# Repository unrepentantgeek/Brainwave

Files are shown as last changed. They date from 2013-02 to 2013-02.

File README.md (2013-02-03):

Description
===========
Brainwave is a low cost controller for Reprap 3D printers derived from the well known Sanguinololu. The primary design goal was lower cost, achieved by providing only the minimum required components for a single extruder printer.  It can be used to drive a cartesian or delta style printer.

Features:
- Small footprint: only 60mm x 79mm!
- 12V power input
- Micro USB connector
- All connectors at edge of board, vertical or right-angle connectors will fit..
- Atmel AT90USB646 microcontroller w/ USB bootloader
- 1, 2, 16 or 32x microstepping @ up to 800mA
- Dual Z-axis connectors
- Optional per channel current attenuation
- Heated bed support with separate power input (up to 24V @ 15A)
- Integrated heater/thermistor/stepper connector for E channel
- Fan control

Instructions
============
1. Build, buy or borrow a Brainwave
2. Install Arduino 1.0.2
3. install the brainwave arduino hardware bundle from
   [github.com/unrepentantgeek/brainwave-arduino](http://github.com/unrepentantgeek/brainwave-arduino)
   into the Arduino hardware directory.
4. Get Marlin. I am maintaining a branch of Marlin that will compile for
   brainwave at [github.com/unrepentantgeek/Marlin](http://github.com/unrepentantgeek/Marlin/tree/brainwave)
   Marlin HEAD has support, but it doesn't always compile cleanly for this
   board.

Hardware configuration
----------------------
1. Set micro-stepping selector jumpers (D1, D2) per channel.  Short both for 32x
   microstepping.  See table on back of board for other configurations.
   <b>Default: single-step.</b>
2. Set stepper current reference voltages.  I = V / 2.55
   <b>Default: 1V == 400mA.</b>

Software configuration
----------------------

Open Arduino, find the Marlin directory and open Marlin.ino. Select 'Brainwave'
from the Board menu. Find the Configuration.h file and change
DEFAULT_AXIS_STEPS_PER_UNIT to suit your printer (remember, 32x microsteps!)
Power on the Brainwave and connect the USB cable (note: the brainwave will not
power up off USB, you need the 12V supply.) Hold down the PROGRAM button and
press RESET, the STATUS led should pulse. Press the Upload button in Arduino.
After a reset the brainwave will show up as a CDC ACM serial device
(/dev/ttyACM[0..9] on Linux) and be ready to accept commands.

Brandon Bowman wrote up an excellent guide for getting the board working under
Windows and MacOS:
[fabbersuw.blogspot.com/2012/12/if-your-brainwaves-got-no-brains-or.html](http://fabbersuw.blogspot.com/2012/12/if-your-brainwaves-got-no-brains-or.html)

Known issues
------------
- It may take a couple of presses of the RESET button to get the firmware to
  come up after flashing.
- You may need a thermistor or similar 100k resistance present across the bed
  and extruder thermistor inputs. Otherwise Marlin may go into a deathloop and
  you'll never even see a serial device. Even if it doesn't fall on it's face it
  will only sit and complain about too high temp.
- Marlin may lose/gain steps on the X axis.  If so swap X and E to limit the
  impact.  This has not been observed with Sprinter.  The issue is being
  investigated.

Special thanks
--------------
Julie Atwood
Matt Westervelt
Frederik Hubinette
Silas Snider
Johann Rocholl
JP Sugarbroad
Austin Appleby
Richard DeLeon
Plamena Milusheva
Mark Ganter
Brandon Bowman

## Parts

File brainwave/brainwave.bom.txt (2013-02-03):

Part     Value             Device             Package         Description                                                            
BED_TEMP                   JP1E               JP1             JUMPER                                                                 
C1       220pF             C-EUC0603          C0603           CAPACITOR, European symbol                                             
C2       10pF              C-EUC0603          C0603           CAPACITOR, European symbol                                             
C3       10pF              C-EUC0603          C0603           CAPACITOR, European symbol                                             
C4       1uF               C-USC0603          C0603           CAPACITOR, American symbol                                             
C5       0.1uF             C-EUC0603          C0603           CAPACITOR, European symbol                                             
C6       0.1uF             C-EUC0603          C0603           CAPACITOR, European symbol                                             
C7       220pF             C-EUC0603          C0603           CAPACITOR, European symbol                                             
C8       10uF              CPOL-US153CLV-0505 153CLV-0505     POLARIZED CAPACITOR, American symbol                                   
C9       0.1uF             C-EUC0603          C0603           CAPACITOR, European symbol                                             
C10      0.1uF             C-EUC0603          C0603           CAPACITOR, European symbol                                             
C11      10uF              CPOL-US153CLV-0505 153CLV-0505     POLARIZED CAPACITOR, American symbol                                   
C12      220pF             C-EUC0603          C0603           CAPACITOR, European symbol                                             
C13      0.1uF             C-EUC0603          C0603           CAPACITOR, European symbol                                             
C14      0.1uF             C-EUC0603          C0603           CAPACITOR, European symbol                                             
C15      10uF              CPOL-US153CLV-0505 153CLV-0505     POLARIZED CAPACITOR, American symbol                                   
C16      220pF             C-EUC0603          C0603           CAPACITOR, European symbol                                             
C17      0.1uF             C-EUC0603          C0603           CAPACITOR, European symbol                                             
C18      0.1uF             C-EUC0603          C0603           CAPACITOR, European symbol                                             
C19      10uF              CPOL-US153CLV-0505 153CLV-0505     POLARIZED CAPACITOR, American symbol                                   
C20      10uF              CPOL-US153CLV-0505 153CLV-0505     POLARIZED CAPACITOR, American symbol                                   
C21      10uF              CPOL-US153CLV-0505 153CLV-0505     POLARIZED CAPACITOR, American symbol                                   
C22      1uF               C-USC0603          C0603           CAPACITOR, American symbol                                             
C23      1uF               C-USC0603          C0603           CAPACITOR, American symbol                                             
C24      0.1uF             C-EUC0603          C0603           CAPACITOR, European symbol                                             
C25      0.1uF             C-EUC0603          C0603           CAPACITOR, European symbol                                             
C26      0.1uF             C-EUC0603          C0603           CAPACITOR, European symbol                                             
C27      0.1uF             C-EUC0603          C0603           CAPACITOR, European symbol                                             
C28      47uF              CPOL-US153CLV-0605 153CLV-0605     POLARIZED CAPACITOR, American symbol                                   
C29      47uF              CPOL-US153CLV-0605 153CLV-0605     POLARIZED CAPACITOR, American symbol                                   
E                          MA04-2             MA04-2          PIN HEADER                                                             
FAN                        JP1E               JP1             JUMPER                                                                 
ICSP                       MA03-2             MA03-2          PIN HEADER                                                             
LED2                       LEDCHIPLED_0805    CHIPLED_0805    LED                                                                    
LED3                       LEDCHIPLED_0805    CHIPLED_0805    LED                                                                    
LED4                       LEDCHIPLED_0805    CHIPLED_0805    LED                                                                    
PROGRAM  PTS645SMT         PTS645SMT          PTS645-SMTR                                                                            
PWR                        LEDCHIPLED_0805    CHIPLED_0805    LED                                                                    
Q1       16MHZ             CRYSTALCSM-3X      CSM-3X          SMD CRYSTAL                                                            
R1       22                R-US_R0603         R0603           RESISTOR, American symbol                                              
R2       22                R-US_R0603         R0603           RESISTOR, American symbol                                              
R3       15k               R-US_R0603         R0603           RESISTOR, American symbol                                              
R4       0.51              R-US_R2512         R2512           RESISTOR, American symbol                                              
R5       0.51              R-US_R2512         R2512           RESISTOR, American symbol                                              
R6       10k               PVZ3A              PVZ3A                                                                                  
R9       15k               R-US_R0603         R0603           RESISTOR, American symbol                                              
R10      0.51              R-US_R2512         R2512           RESISTOR, American symbol                                              
R11      0.51              R-US_R2512         R2512           RESISTOR, American symbol                                              
R12      10k               PVZ3A              PVZ3A                                                                                  
R15      15k               R-US_R0603         R0603           RESISTOR, American symbol                                              
R16      0.51              R-US_R2512         R2512           RESISTOR, American symbol                                              
R17      0.51              R-US_R2512         R2512           RESISTOR, American symbol                                              
R18      10k               PVZ3A              PVZ3A                                                                                  
R21      15k               R-US_R0603         R0603           RESISTOR, American symbol                                              
R22      0.51              R-US_R2512         R2512           RESISTOR, American symbol                                              
R23      0.51              R-US_R2512         R2512           RESISTOR, American symbol                                              
R24      10k               PVZ3A              PVZ3A                                                                                  
R27      10r               R-US_R0603         R0603           RESISTOR, American symbol                                              
R28      100k              R-US_R0603         R0603           RESISTOR, American symbol                                              
R29      1.8k              R-US_R0603         R0603           RESISTOR, American symbol                                              
R30      10r               R-US_R0603         R0603           RESISTOR, American symbol                                              
R31      100k              R-US_R0603         R0603           RESISTOR, American symbol                                              
R32      1.8k              R-US_R0603         R0603           RESISTOR, American symbol                                              
R33      1k                R-US_R0603         R0603           RESISTOR, American symbol                                              
R34      4.7k              R-US_R0603         R0603           RESISTOR, American symbol                                              
R35      4.7k              R-US_R0603         R0603           RESISTOR, American symbol                                              
R36      10k               R-US_R0603         R0603           RESISTOR, American symbol                                              
R37      10r               R-US_R0603         R0603           RESISTOR, American symbol                                              
R38      100k              R-US_R0603         R0603           RESISTOR, American symbol                                              
R39      1.8k              R-US_R0603         R0603           RESISTOR, American symbol                                              
R40      1k                R-US_R0603         R0603           RESISTOR, American symbol                                              
RESET    PTS645SMT         PTS645SMT          PTS645-SMTR                                                                            
STAT                       LEDCHIPLED_0805    CHIPLED_0805    LED                                                                    
U1       AT90USB64/128     AT90USB64/128      TQFP64                                                                                 
U2       LV8713T           LV8713T            TSSOP24         PWM Constant-Current Control Stepping Motor Driver                     
U3       LV8713T           LV8713T            TSSOP24         PWM Constant-Current Control Stepping Motor Driver                     
U4       LV8713T           LV8713T            TSSOP24         PWM Constant-Current Control Stepping Motor Driver                     
U5       LV8713T           LV8713T            TSSOP24         PWM Constant-Current Control Stepping Motor Driver                     
U6       7805              78*                SOT89                                                                                  
U7       IRF8313PBF        IRF8313PBF         SO8                                                                                    
U8       IRF8313PBF        IRF8313PBF         SO8                                                                                    
X                          MA04-1             MA04-1          PIN HEADER                                                             
X1                         W237-102           W237-102        WAGO SCREW CLAMP                                                       
X2                         W237-102           W237-102        WAGO SCREW CLAMP                                                       
X3                         W237-102           W237-102        WAGO SCREW CLAMP                                                       
X5       MICRO-USB-SHIELD- MICRO-USB-SHIELD-  10118192-0001LF MINI USB Connector                                                     
X_MIN                      JP1E               JP1             JUMPER                                                                 
Y                          MA04-1             MA04-1          PIN HEADER                                                             
Y_MIN                      JP1E               JP1             JUMPER                                                                 
Z                          MA04-2             MA04-2          PIN HEADER                                                             
Z_MIN                      JP1E               JP1             JUMPER

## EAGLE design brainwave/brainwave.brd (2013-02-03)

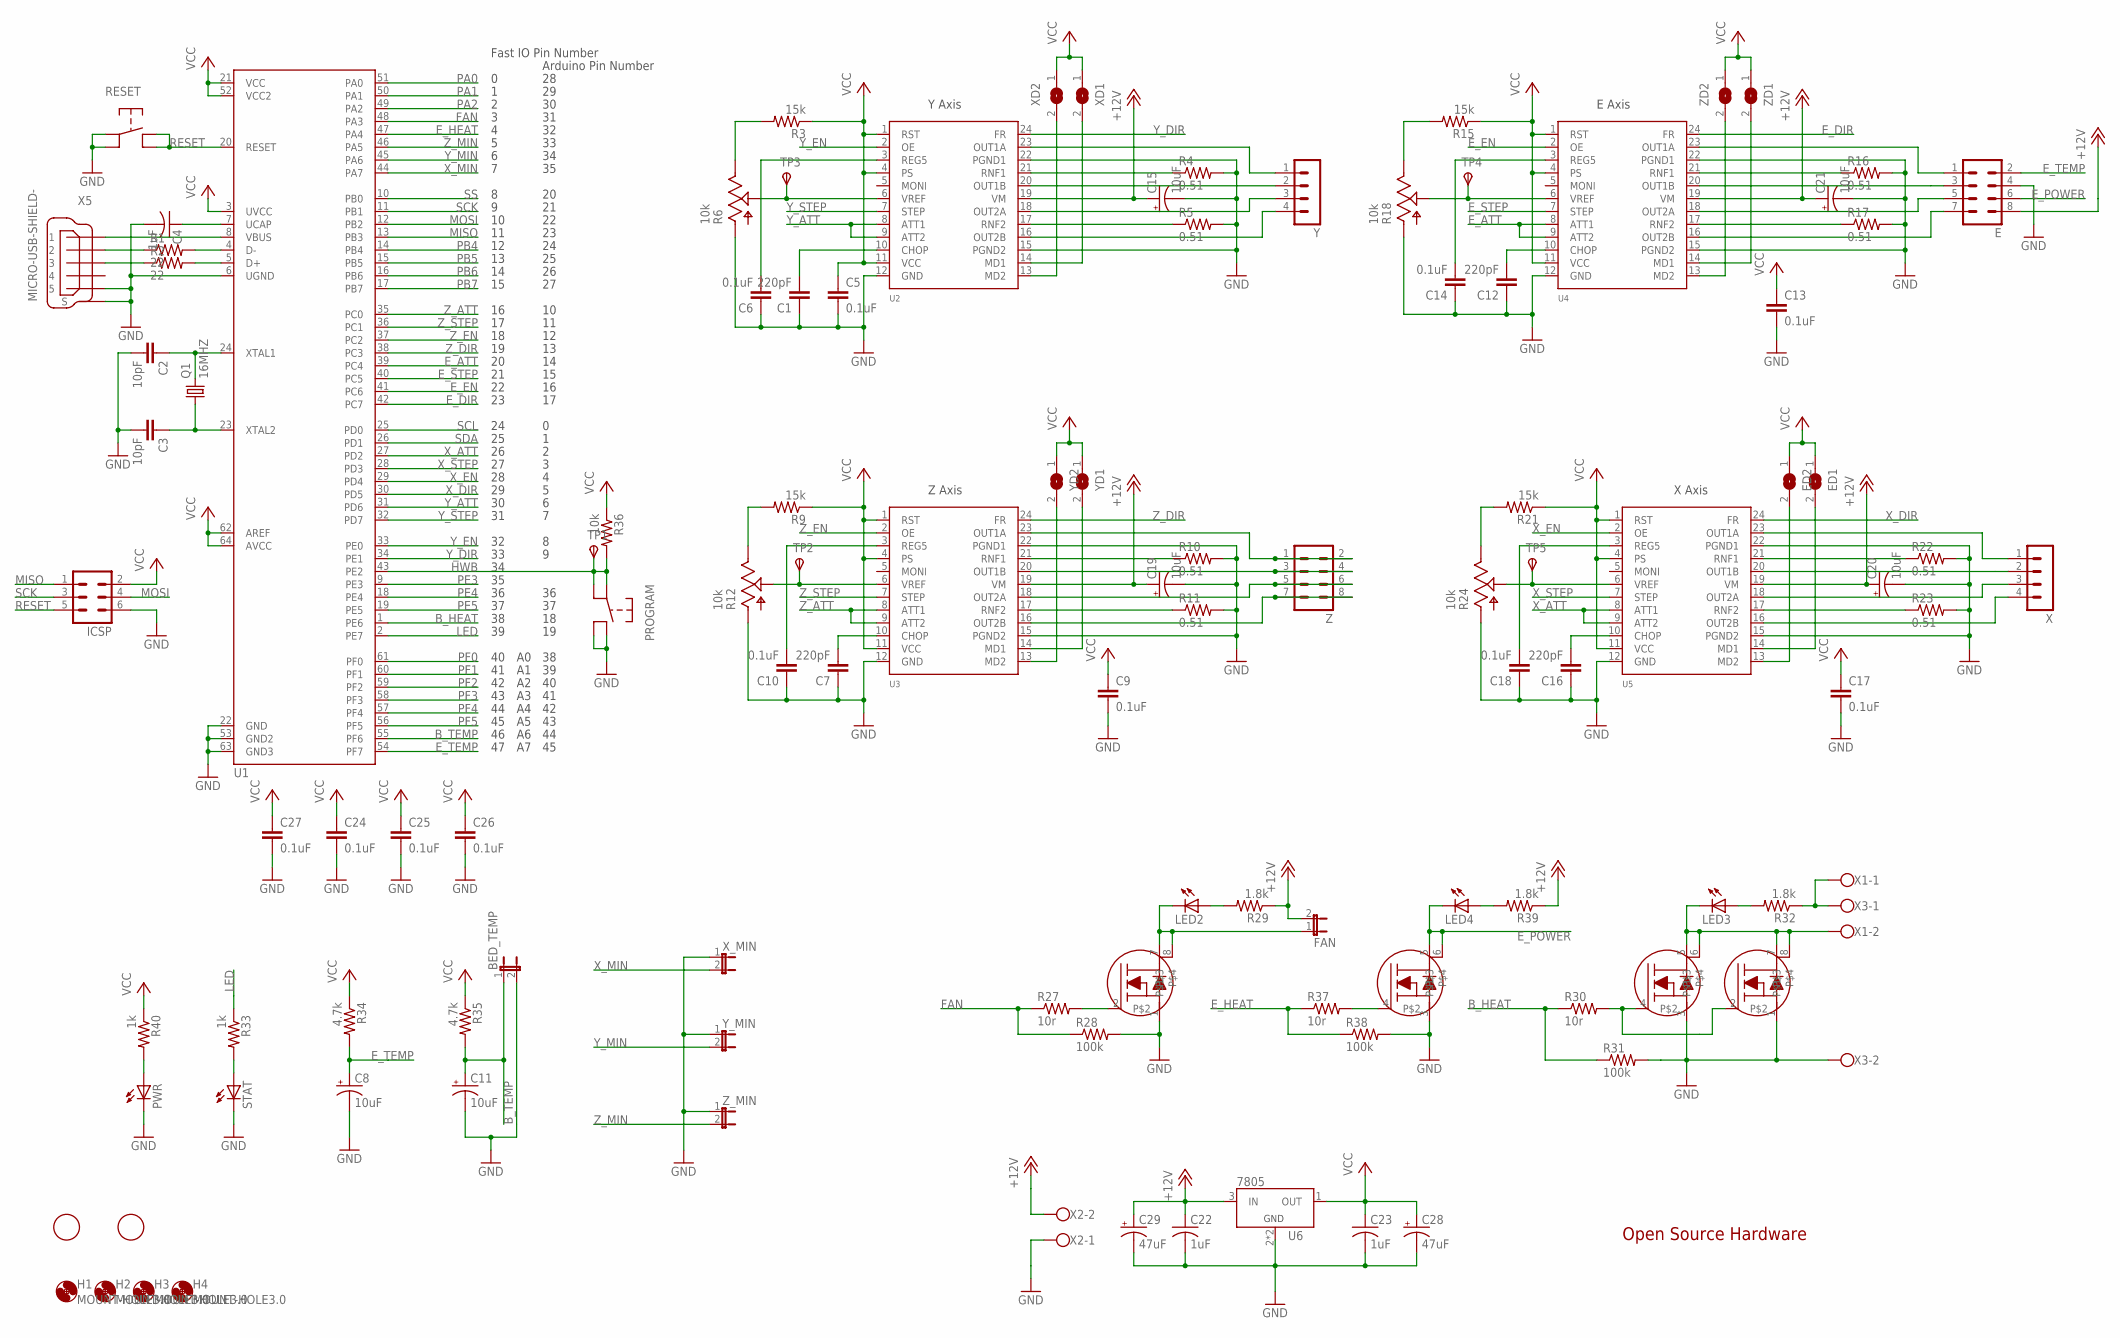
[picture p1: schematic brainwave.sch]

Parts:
BED_TEMP: JP1E; JP1
C1, C7, C12, C16: 220pF; C0603
C2, C3: 10pF; C0603
C4, C22, C23: 1uF; C0603
C5, C6, C9, C10, C13, C14, C17, C18, C24, C25, C26, C27: 0.1uF; C0603
C8, C11, C15, C19, C20, C21: 10uF; 153CLV-0505
C28, C29: 47uF; 153CLV-0605
E: MA04-2
ED1, ED2: SJ
FAN: JP1E; JP1
H1, H2, H3, H4: MOUNT-HOLE3.0; 3,0
ICSP: MA03-2
LED2, LED3, LED4: LEDCHIPLED_0805; CHIPLED_0805
PROGRAM: PTS645SMT; PTS645-SMTR
PWR: LEDCHIPLED_0805; CHIPLED_0805
Q1: 16MHZ; CSM-3X
R1, R2: 22; R0603
R3, R9, R15, R21: 15k; R0603
R4, R5, R10, R11, R16, R17, R22, R23: 0.51; R2512
R6, R12, R18, R24: 10k; PVZ3A
R27, R30, R37: 10r; R0603
R28, R31, R38: 100k; R0603
R29, R32, R39: 1.8k; R0603
R33, R40: 1k; R0603
R34, R35: 4.7k; R0603
R36: 10k; R0603
RESET: PTS645SMT; PTS645-SMTR
STAT: LEDCHIPLED_0805; CHIPLED_0805
TP1, TP2, TP3, TP4, TP5: TPSTP08R; TP08R
U1: AT90USB64/128; TQFP64
U2, U3, U4, U5: LV8713T; TSSOP24
U6: 7805; SOT89
U7, U8: IRF8313PBF; SO8
U$1, U$2: FIDUCIAL; FIDUCIAL_1MM
X: MA04-1
X1, X3: W237-102; MPN 237-102
X2: W237-102
X5: MICRO-USB-SHIELD-; 10118192-0001LF
XD1, XD2: SJ
X_MIN: JP1E; JP1
Y: MA04-1
YD1, YD2: SJ
Y_MIN: JP1E; JP1
Z: MA04-2
ZD1, ZD2: SJ
Z_MIN: JP1E; JP1

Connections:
+12V: C15.+, C19.+, C20.+, C21.+, C22.1, C29.+, E.8, FAN.2, R29.1, R39.1, U2.19 (VM), U3.19 (VM), U4.19 (VM), U5.19 (VM), U6.3 (IN), X2.2
BED_POWER: R32.1, X1.1, X3.1
B_HEAT: R30.1, R31.1, U1.1 (PE6)
B_TEMP: BED_TEMP.1, C11.+, R35.2, U1.55 (PF6)
E_ATT: U1.39 (PC4), U4.8 (ATT1), U4.9 (ATT2)
E_DIR: U1.42 (PC7), U4.24 (FR)
E_EN: U1.41 (PC6), U4.2 (OE)
E_HEAT: R37.1, R38.1, U1.47 (PA4)
E_POWER: E.6, LED4.C, U7.5, U7.6
E_STEP: U1.40 (PC5), U4.7 (STEP)
E_TEMP: C8.+, E.2, R34.2, U1.54 (PF7)
FAN: R27.1, R28.1, U1.48 (PA3)
GND: BED_TEMP.2, C1.1, C2.2, C3.2, C4.2, C5.2, C6.1, C7.1, C8.-, C9.2, C10.1, C11.-, C12.1, C13.2, C14.1, C15.-, C16.1, C17.2, C18.1, C19.-, C20.-, C21.-, C22.2, C23.2, C24.2, C25.2, C26.2, C27.2, C28.-, C29.-, E.4, ICSP.6, PROGRAM.P$3, PROGRAM.P$4, PWR.C, R4.2, R5.2, R6.P$1, R10.2, R11.2, R12.P$1, R16.2, R17.2, R18.P$1, R22.2, R23.2, R24.P$1, R28.2, R31.2, R38.2, RESET.P$1, RESET.P$2, STAT.C, U1.6 (UGND), U1.22 (GND), U1.53 (GND2), U1.63 (GND3), U2.12 (GND), U2.15 (PGND2), U2.22 (PGND1), U3.12 (GND), U3.15 (PGND2), U3.22 (PGND1), U4.12 (GND), U4.15 (PGND2), U4.22 (PGND1), U5.12 (GND), U5.15 (PGND2), U5.22 (PGND1), U6.2 (GND), U6.2@1 (GND), U7.1, U7.3, U8.1, U8.3, X2.1, X3.2, X5.5, X5.M1 (S), X5.M2 (S), X5.M3 (S), X5.M4 (S), X5.M5 (S), X5.M6 (S), X_MIN.1, Y_MIN.1, Z_MIN.1
HWB: PROGRAM.P$1, PROGRAM.P$2, R36.2, TP1.TP, U1.43 (PE2)
LED: R33.1, U1.2 (PE7)
MISO: ICSP.1, U1.13 (PB3)
MOSI: ICSP.4, U1.12 (PB2)
unnamed: U1.8 (VBUS), X5.1
unnamed: R1.1, X5.2
unnamed: R2.1, X5.3
unnamed: U3.20 (OUT1B), Z.3, Z.4
unnamed: C4.1, U1.7 (UCAP)
unnamed: C2.1, Q1.2, U1.24 (XTAL1)
unnamed: C3.1, Q1.1, U1.23 (XTAL2)
unnamed: R6.P$2, TP3.TP, U2.6 (VREF)
unnamed: R4.1, U2.21 (RNF1)
unnamed: R5.1, U2.17 (RNF2)
unnamed: U2.16 (OUT2B), Y.4
unnamed: U2.18 (OUT2A), Y.3
unnamed: U2.20 (OUT1B), Y.2
unnamed: U2.23 (OUT1A), Y.1
unnamed: C1.2, U2.10 (CHOP)
unnamed: C6.2, U2.3 (REG5)
unnamed: R3.2, R6.P$3
unnamed: U2.13 (MD2), XD2.2
unnamed: U2.14 (MD1), XD1.2
unnamed: R30.2, U8.2, U8.4
unnamed: R10.1, U3.21 (RNF1)
unnamed: R11.1, U3.17 (RNF2)
unnamed: U3.16 (OUT2B), Z.7, Z.8
unnamed: U3.18 (OUT2A), Z.5, Z.6
unnamed: U3.23 (OUT1A), Z.1, Z.2
unnamed: C7.2, U3.10 (CHOP)
unnamed: C10.2, U3.3 (REG5)
unnamed: R12.P$2, TP2.TP, U3.6 (VREF)
unnamed: R9.2, R12.P$3
unnamed: U3.13 (MD2), YD2.2
unnamed: U3.14 (MD1), YD1.2
unnamed: R33.2, STAT.A
unnamed: R37.2, U7.4
unnamed: LED4.A, R39.2
unnamed: PWR.A, R40.2
unnamed: R16.1, U4.21 (RNF1)
unnamed: R17.1, U4.17 (RNF2)
unnamed: E.7, U4.16 (OUT2B)
unnamed: E.5, U4.18 (OUT2A)
unnamed: E.3, U4.20 (OUT1B)
unnamed: E.1, U4.23 (OUT1A)
unnamed: C12.2, U4.10 (CHOP)
unnamed: C14.2, U4.3 (REG5)
unnamed: R18.P$2, TP4.TP, U4.6 (VREF)
unnamed: R15.2, R18.P$3
unnamed: U4.13 (MD2), ZD2.2
unnamed: U4.14 (MD1), ZD1.2
unnamed: R22.1, U5.21 (RNF1)
unnamed: R23.1, U5.17 (RNF2)
unnamed: U5.16 (OUT2B), X.4
unnamed: U5.18 (OUT2A), X.3
unnamed: U5.20 (OUT1B), X.2
unnamed: U5.23 (OUT1A), X.1
unnamed: C16.2, U5.10 (CHOP)
unnamed: C18.2, U5.3 (REG5)
unnamed: R24.P$2, TP5.TP, U5.6 (VREF)
unnamed: R21.2, R24.P$3
unnamed: ED2.2, U5.13 (MD2)
unnamed: ED1.2, U5.14 (MD1)
unnamed: R27.2, U7.2
unnamed: LED2.A, R29.2
unnamed: FAN.1, LED2.C, U7.7, U7.8
unnamed: LED3.C, U8.5, U8.6, U8.7, U8.8, X1.2
unnamed: LED3.A, R32.2
PA0: U1.51 (PA0)
PA1: U1.50 (PA1)
PA2: U1.49 (PA2)
PB4: U1.14 (PB4)
PB5: U1.15 (PB5)
PB6: U1.16 (PB6)
PB7: U1.17 (PB7)
PE3: U1.9 (PE3)
PE4: U1.18 (PE4)
PE5: U1.19 (PE5)
PF0: U1.61 (PF0)
PF1: U1.60 (PF1)
PF2: U1.59 (PF2)
PF3: U1.58 (PF3)
PF4: U1.57 (PF4)
PF5: U1.56 (PF5)
RESET: ICSP.5, RESET.P$3, RESET.P$4, U1.20 (RESET)
SCK: ICSP.3, U1.11 (PB1)
SCL: U1.25 (PD0)
SDA: U1.26 (PD1)
SS: U1.10 (PB0)
USB1_N: R1.2, U1.4 (D-)
USB1_P: R2.2, U1.5 (D+)
VCC: C5.1, C9.1, C13.1, C17.1, C23.1, C24.1, C25.1, C26.1, C27.1, C28.+, ED1.1, ED2.1, ICSP.2, R3.1, R9.1, R15.1, R21.1, R34.1, R35.1, R36.1, R40.1, U1.3 (UVCC), U1.21 (VCC), U1.52 (VCC2), U1.62 (AREF), U1.64 (AVCC), U2.1 (RST), U2.4 (PS), U2.11 (VCC), U3.1 (RST), U3.4 (PS), U3.11 (VCC), U4.1 (RST), U4.4 (PS), U4.11 (VCC), U5.1 (RST), U5.4 (PS), U5.11 (VCC), U6.1 (OUT), XD1.1, XD2.1, YD1.1, YD2.1, ZD1.1, ZD2.1
X_ATT: U1.27 (PD2), U5.8 (ATT1), U5.9 (ATT2)
X_DIR: U1.30 (PD5), U5.24 (FR)
X_EN: U1.29 (PD4), U5.2 (OE)
X_MIN: U1.44 (PA7), X_MIN.2
X_STEP: U1.28 (PD3), U5.7 (STEP)
Y_ATT: U1.31 (PD6), U2.8 (ATT1), U2.9 (ATT2)
Y_DIR: U1.34 (PE1), U2.24 (FR)
Y_EN: U1.33 (PE0), U2.2 (OE)
Y_MIN: U1.45 (PA6), Y_MIN.2
Y_STEP: U1.32 (PD7), U2.7 (STEP)
Z_ATT: U1.35 (PC0), U3.8 (ATT1), U3.9 (ATT2)
Z_DIR: U1.38 (PC3), U3.24 (FR)
Z_EN: U1.37 (PC2), U3.2 (OE)
Z_MIN: U1.46 (PA5), Z_MIN.2
Z_STEP: U1.36 (PC1), U3.7 (STEP)

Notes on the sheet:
E Axis
Z Axis
X Axis
Y Axis
Fast IO Pin Number
Open Source Hardware
Arduino Pin Number

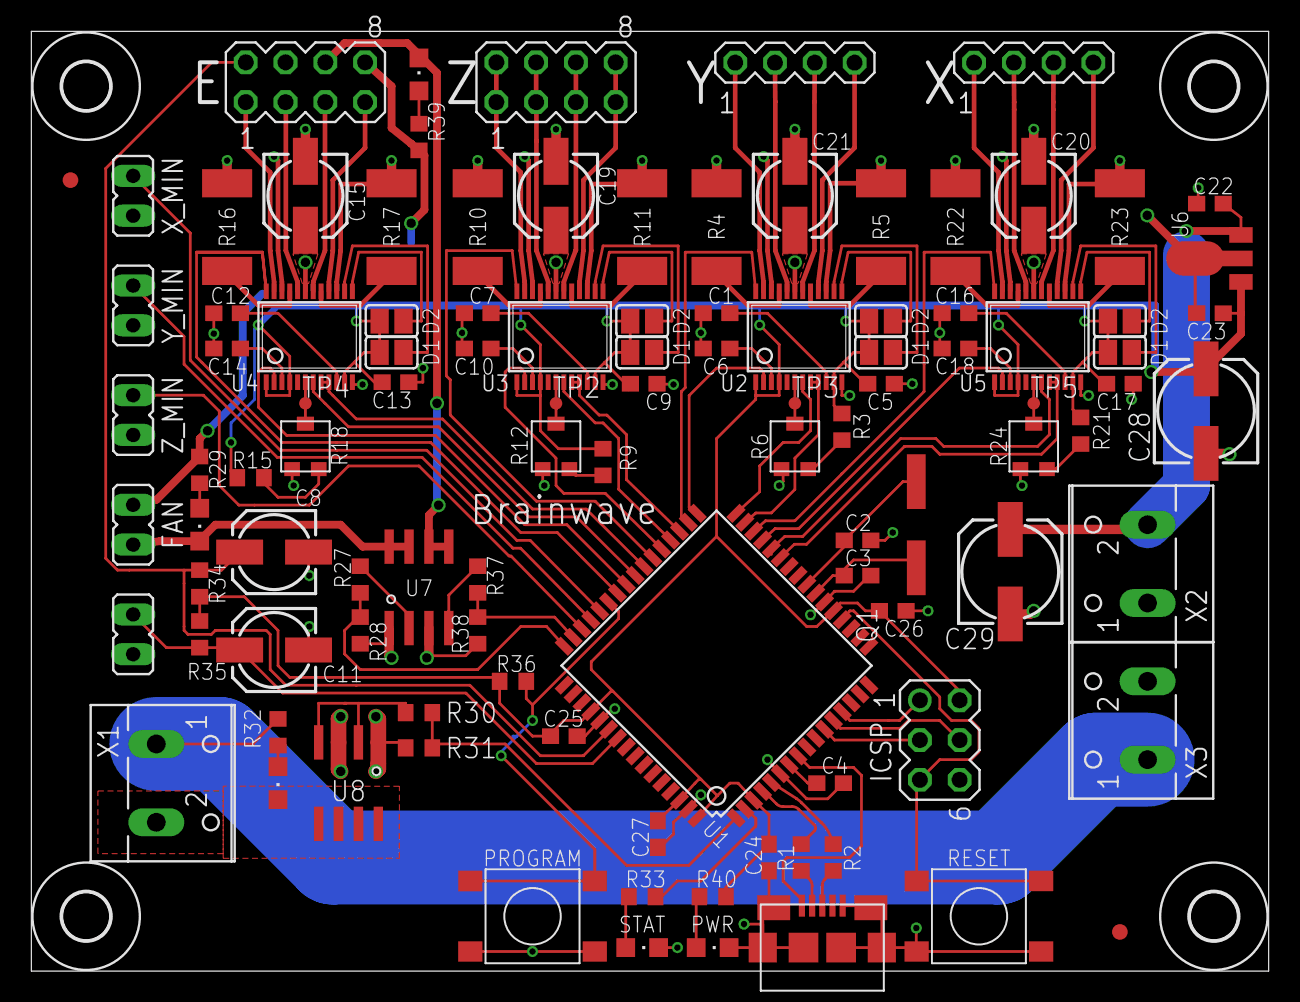
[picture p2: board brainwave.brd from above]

Board: 2 copper layers, 79.0 x 60.0 mm, 110 parts (1 on the bottom side), 101 nets.

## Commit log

2012-12-11 Version 1.0 final schematic and board files
    [brainwave.brd, brainwave.sch]
2013-02-03 Update readme add BOM put license in silk
    [brainwave.brd]

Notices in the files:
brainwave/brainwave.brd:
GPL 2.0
